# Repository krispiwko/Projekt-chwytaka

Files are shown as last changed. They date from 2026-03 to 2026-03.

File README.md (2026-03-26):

Autor: Krzysztof Piwkowski

Opis projektu:
Chwytak wykonany na zajęcia z Prototypowania konstrukcji w technice druku 3D i CNC.
Schemat chwytaka dostarczony od prowadzącego zajęcia. Chwytak ma za zadanie
podnieść drewniany obiekt w kształcie walca o średnicy 60mm i wysokości 150mm.
Do zaprojektowania struktury fizycznej został wykorzystany program Autodesk Inventor.
Obliczenia funkcji kinematycznych wykonano w Matlabie. Widok chwytaka można odtworzyć
kopiując pliki z folderu "Pliki chwytaka" do darmowego viewera firmy autodesk:
viewer.autodesk.com
Szczegółowe informacje znajdują się w sprawozdaniu zamieszczonym na repozytorium.

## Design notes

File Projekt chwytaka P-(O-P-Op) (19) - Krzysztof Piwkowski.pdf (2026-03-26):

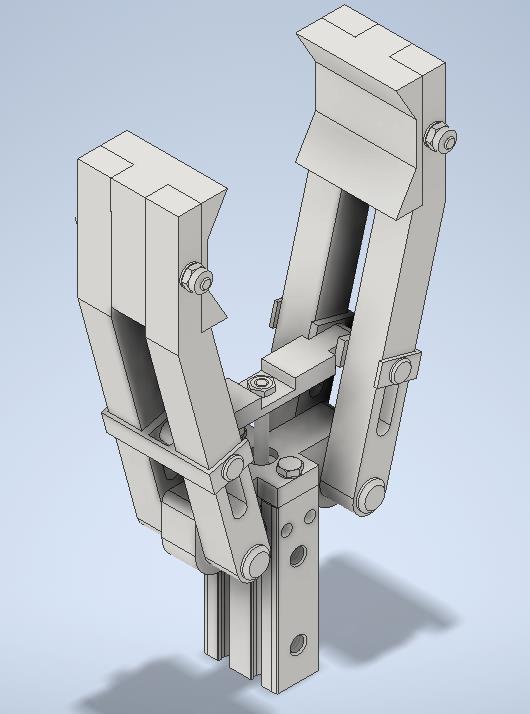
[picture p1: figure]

# PROJEKT CHWYTAKA P-(O-P-Op)

## Jednostka: AGH WEAIIB – Automatyka i Robotyka – Gr. 7

Data wykonania: 7 czerwca 2024r.

## Autor: Krzysztof Piwkowski

## Spis treści

## 1. O projekcie

Przedstawiony w tym projekcie chwytak był wykonany według podanego poniżej schematu:

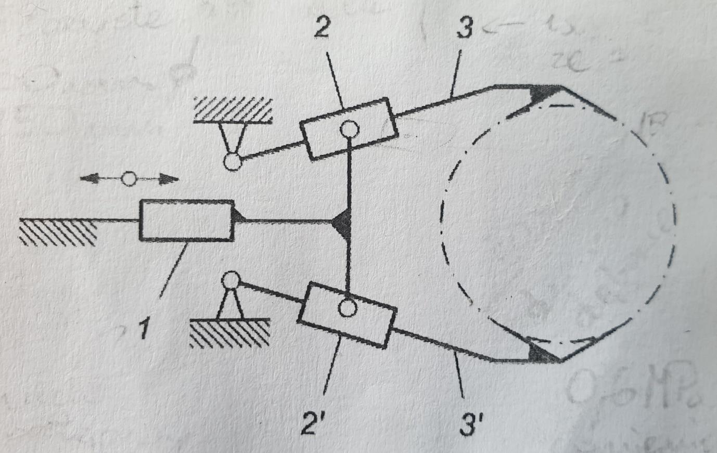
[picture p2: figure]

Chwytak ma parametry przystosowane do podnoszenia przedmiotu z powietrzosuchego drewna dębowego w kształcie walca o średnicy 60mm i wysokości 150mm. Jest to chwytak siłowo-kształtowy o siłowniku postępowym z parami kinematycznymi – obrotowej, postępowej i prowadnicy z możliwością obrotu (P-(O-P-Op)). Ostatecznie ruch szczęki chwytaka prowadzony jest po okręgu. Znając te informacje oraz ilość użytych w projekcie par kinematycznych możemy dokonać analizy ruchliwości chwytaka:

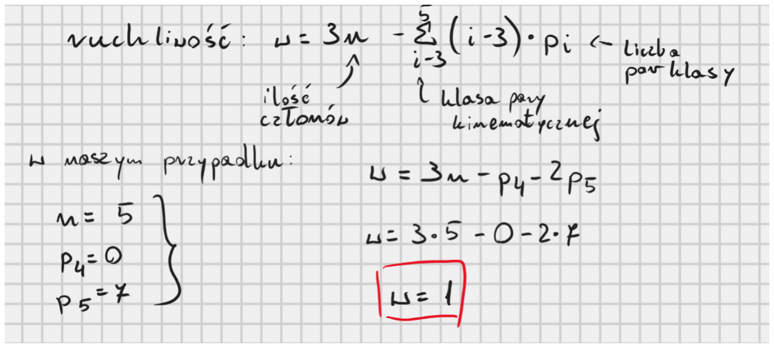
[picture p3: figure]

Ruchliwość rzędu 1 oznacza, że wprawienie w ruch jednego członu wprawia w ruch pozostałe.

## 2. Analiza geometryczna

Aby dokonać analizy geometrycznej wykonałem schemat chwytaka w rozmiarze rzeczywistym. Następnie wyznaczyłem minimalny kąt wychylenia potrzebny na wypuszczenie przedmiotu, co pozwoliło wyznaczyć skok siłownika:

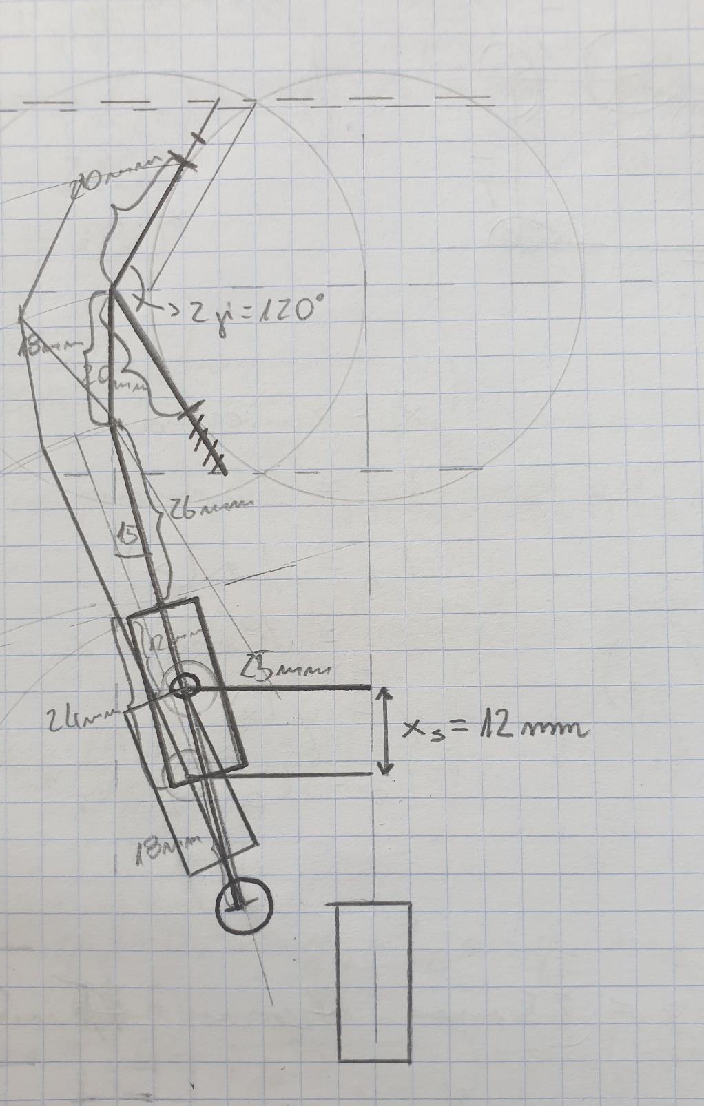
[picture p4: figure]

Analiza geometryczna pozwoliła wyznaczyć skok siłownika na 12mm, jednak najczęściej dostępne są jedynie siłowniki o skoku 10 lub 15mm. Aby przedmiot mógł swobodnie wypaść, należało wybrać siłownik o większym skoku – 15mm. Rysunek pozwolił także przyjąć długości odpowiednich elementów chwytaka oraz kąt rozstawienia szczęki (zaznaczone na rysunku).

## 3. Charakterystyka siłowa

Charakterystyka siłowa polegała na związanie ze sobą sił działających na poszczególne elementy chwytaka tak, aby przenieść siłę chwytu na siłę siłownika. Parametry potrzebne do wyznaczenia odpowiednich wartości przyjęto jako:

- współczynnik tarcia stal – drewno: 0,55 [1]
- gęstość drewna dębowego minimalna i maksymalna: 710 i 800 kg/m^3 [2] Wyznaczenie minimalnej siły chwytu, aby bezpiecznie utrzymać obiekt prezentuje się następująco:

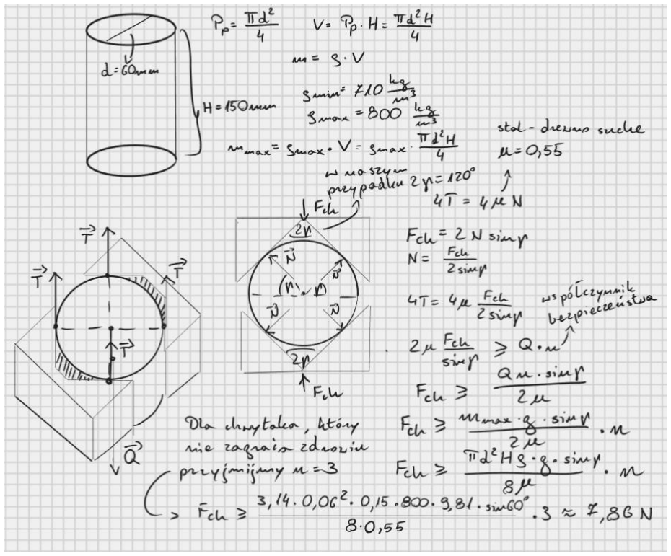
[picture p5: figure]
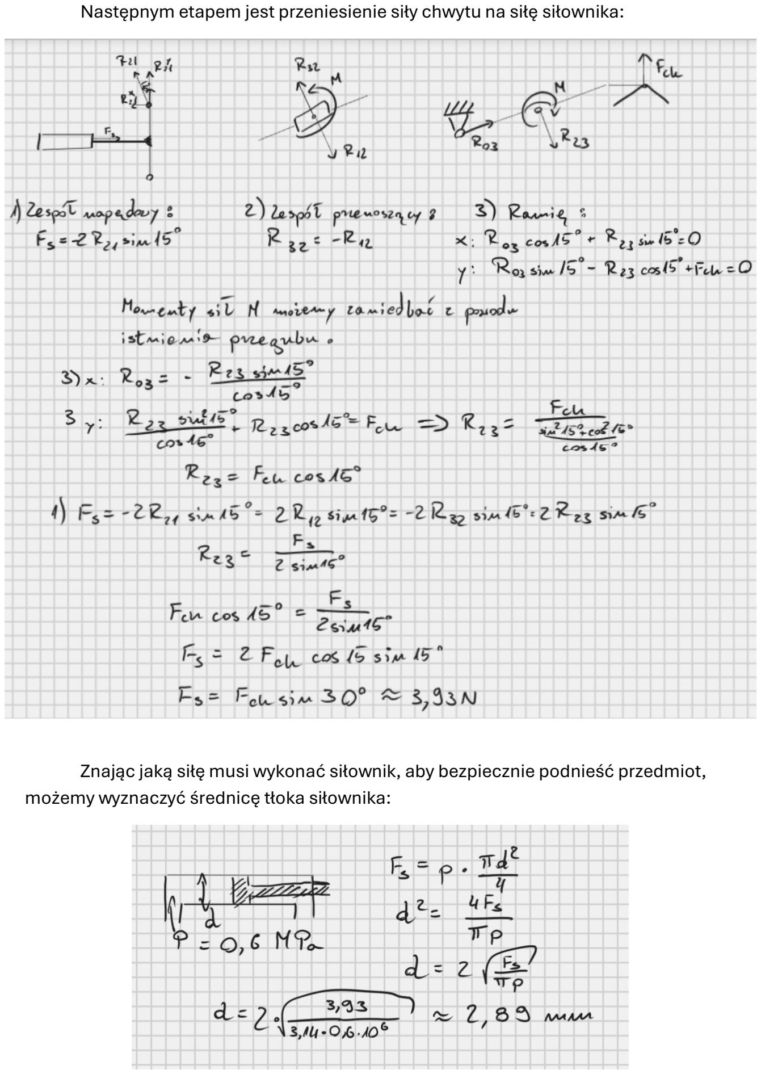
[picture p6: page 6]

Następnym etapem jest przeniesienie siły chwytu na siłę siłownika:

Znając jaką siłę musi wykonać siłownik, aby bezpiecznie podnieść przedmiot, możemy wyznaczyć średnicę tłoka siłownika:

Znając skok (15mm) i średnicę tłoka(2,89mm) możemy przejść do dobrania odpowiedniego siłownika. Wybierając kompaktowy siłownik, który jest łatwy w montażu, o skoku 15mm okazuje się, że dostępny model jest tylko o średnicy tłoka od 6mm. Wybierając siłownik o takiej średnicy zwiększamy siłę chwytu czterokrotnie. Dlatego przyjęty na początku współczynnik bezpieczeństwa także zwiększy się czterokrotnie (n = 12).
Ostatecznie wybrany przeze mnie chwytak można znaleźć na stronie internetowej Festo:

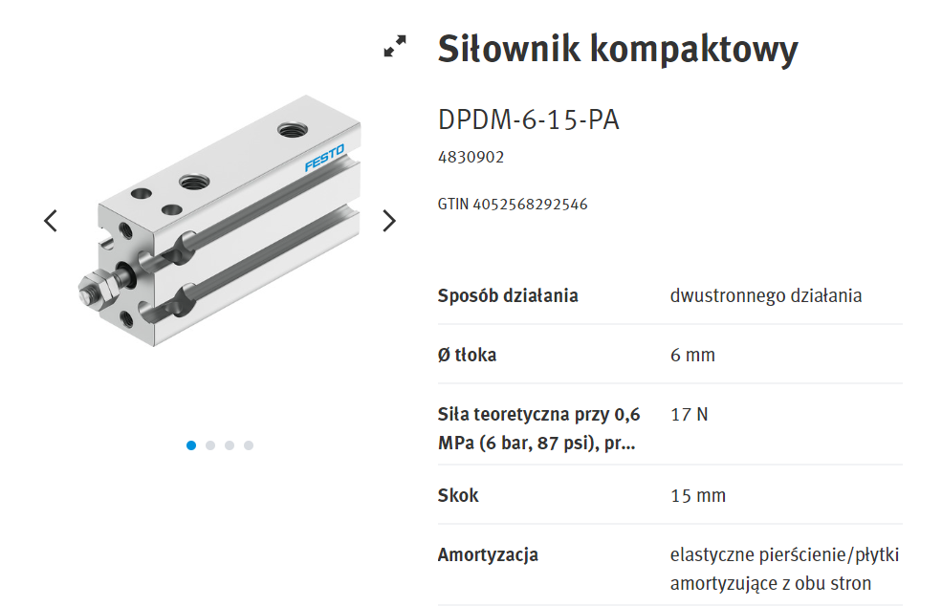
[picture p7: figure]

Znając już, jaki model chwytaka będzie użyty, można przejść do utworzenia ostatecznego modelu całego chwytaka. Do zbudowania chwytaka użyłem programu Autodesk Inventor. Model 3D widnieje na stronie tytułowej, tutaj zamieszczony zostaje rysunek złożeniowy:

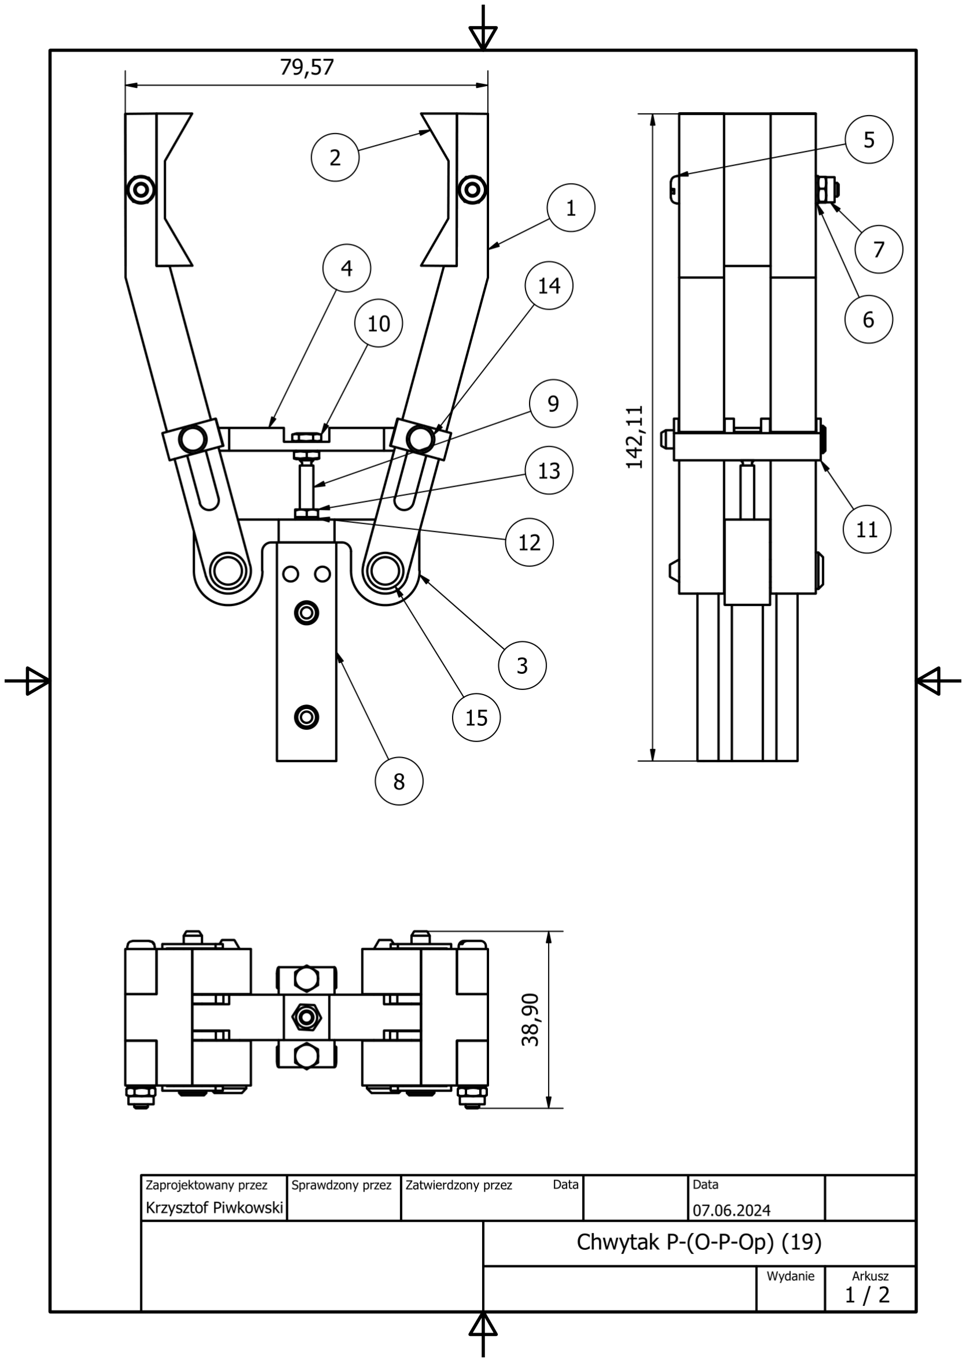
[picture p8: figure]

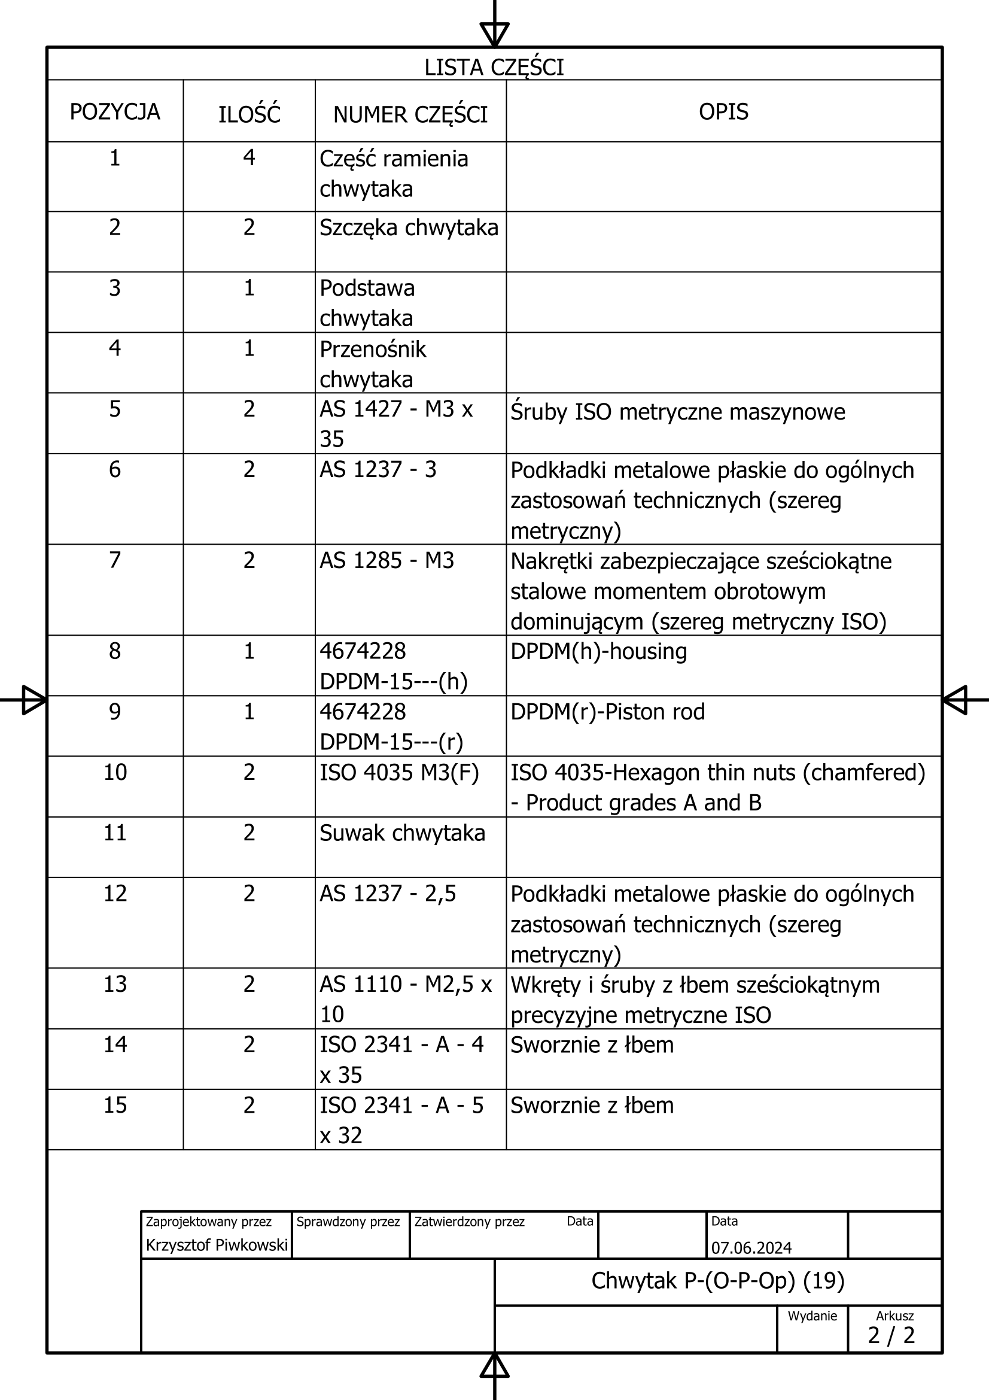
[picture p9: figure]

## 4. Charakterystyka przesunięciowa i prędkościowa

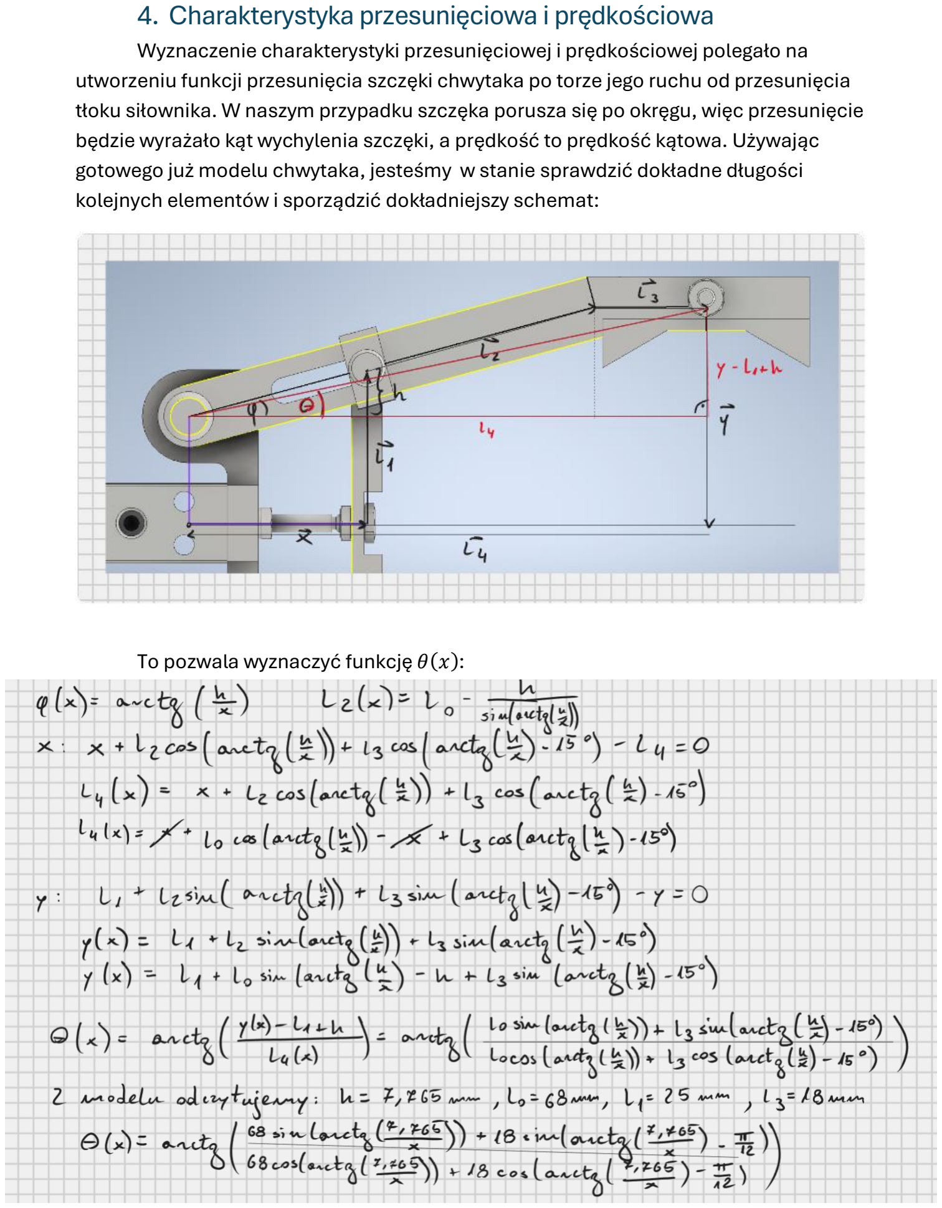
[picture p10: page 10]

Wyznaczenie charakterystyki przesunięciowej i prędkościowej polegało na utworzeniu funkcji przesunięcia szczęki chwytaka po torze jego ruchu od przesunięcia tłoku siłownika. W naszym przypadku szczęka porusza się po okręgu, więc przesunięcie będzie wyrażało kąt wychylenia szczęki, a prędkość to prędkość kątowa. Używając gotowego już modelu chwytaka, jesteśmy w stanie sprawdzić dokładne długości kolejnych elementów i sporządzić dokładniejszy schemat:

To pozwala wyznaczyć funkcję θ(x):

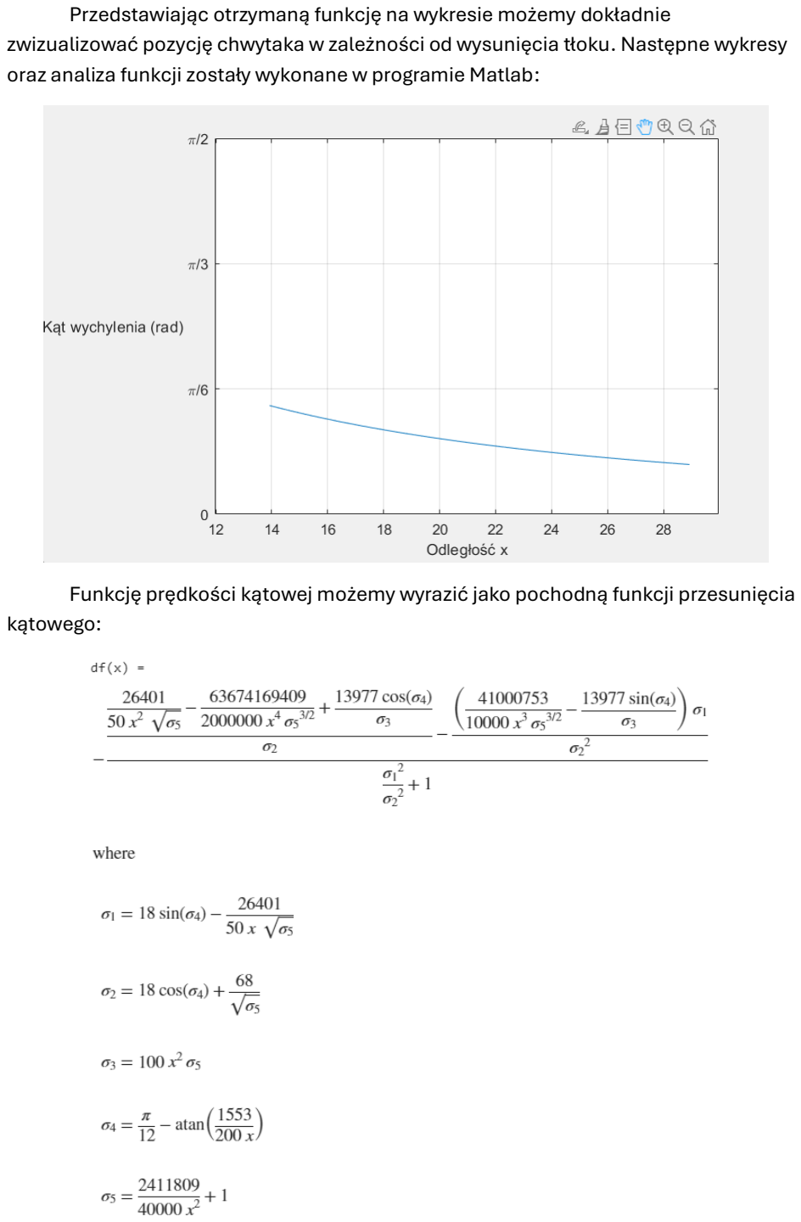
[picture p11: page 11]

Przedstawiając otrzymaną funkcję na wykresie możemy dokładnie zwizualizować pozycję chwytaka w zależności od wysunięcia tłoku. Następne wykresy oraz analiza funkcji zostały wykonane w programie Matlab:

Funkcję prędkości kątowej możemy wyrazić jako pochodną funkcji przesunięcia kątowego:

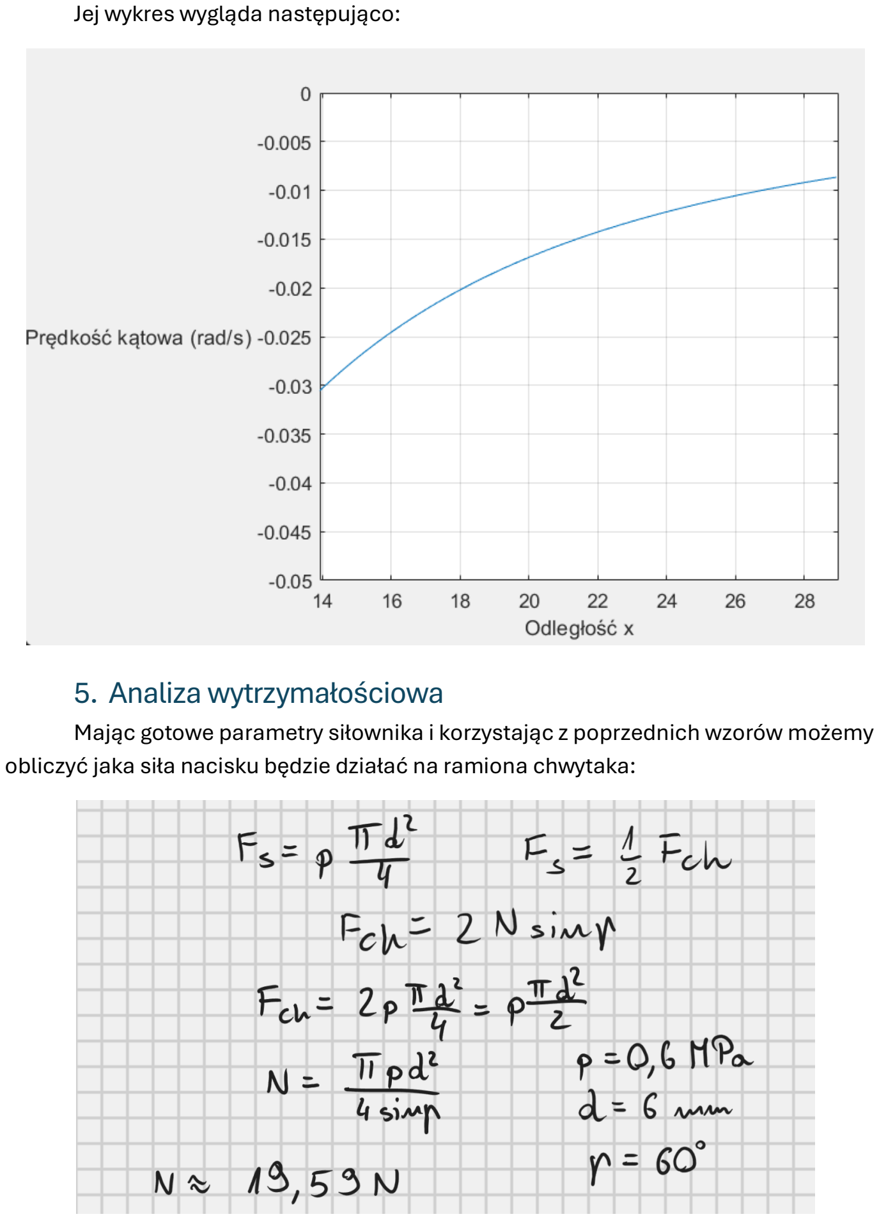
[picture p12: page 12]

Jej wykres wygląda następująco:

## 5. Analiza wytrzymałościowa

Mając gotowe parametry siłownika i korzystając z poprzednich wzorów możemy obliczyć jaka siła nacisku będzie działać na ramiona chwytaka:

Korzystając z obliczonej siły wykonajmy analizę naprężeń w programie Inventor:

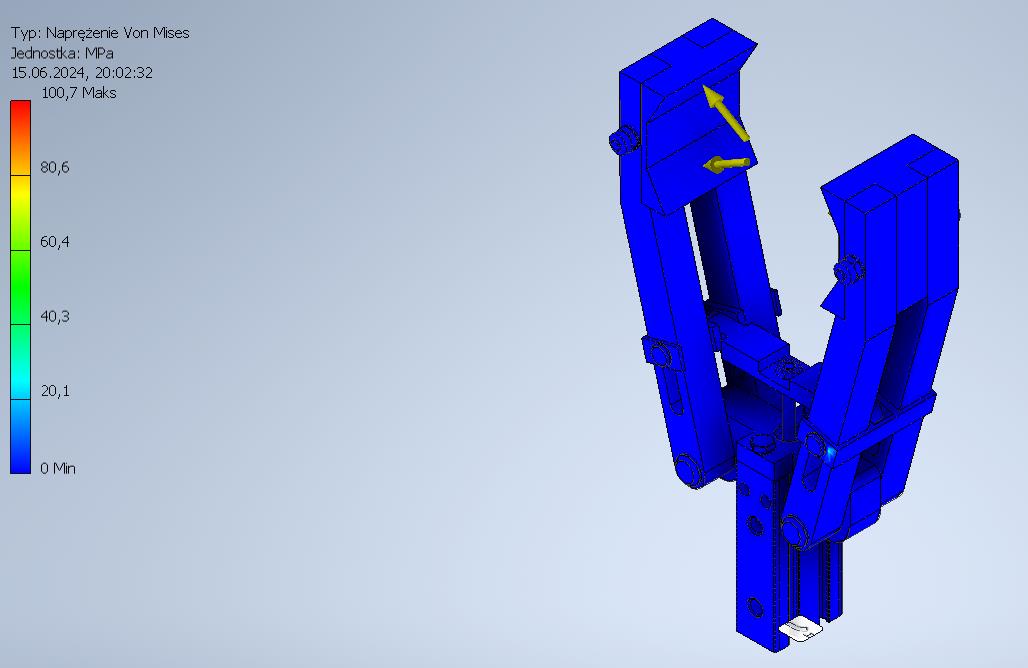
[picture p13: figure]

Jak widać na skali po lewej stronie, maksimum naprężeń wynosi 100,7MPa, podczas gdy wartości współczynników wytrzymałościowych stali węglowej, z jakiej wykonany jest chwytak, prezentują się następująco:

Informacje te znajdują się jako domyślne wartości w programie Inventor. Widać zatem, że generowane naprężenia nie spowodują uszkodzenia chwytaka.
Możemy także zbadać czy siła nacisku, jaką chwytak wywiera na przedmiot, spowoduje uszkodzenie drewna dębowego. Aby to zrobić, przyjmijmy, że szerokość pola powierzchni styczności między okrągłym przedmiotem a szczęką to 1mm, podczas gdy długość szczęki wynosi 30mm. Wówczas:

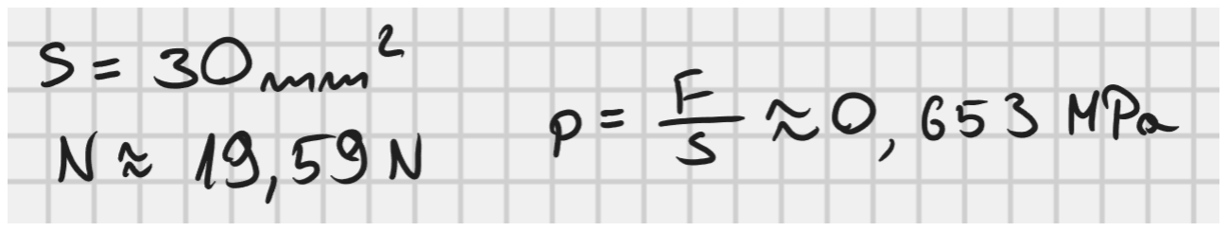
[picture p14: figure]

Wytrzymałość drewna dębowego w najgorszym przypadku wynosi 11MPa [3], więc siła nacisku nie uszkodzi materiału.

## 6. Parametry

Ostateczne zestawienie najważniejszych parametrów związanych z pracą chwytaka:

Średnica
tłoka [mm]

Czynnik
roboczy

Ciśnienie pracy
[MPa]
Siła chwytu [N] | Typ chwytaka | Promień podnoszonego
obiektu walcowego [mm]
6 powietrze | 0,6 | 33,93 siłowo - kstzałtowy | 60
Minimalne wychylenie kątowe [°] | Maksymalne wychylenie kątowe [°] | Minimalna odległość szczęki od środka [mm] | Maksymalna odległość szczęki od środka [mm]
11,9 | 26 | 34,87 | 54,72

## 7. Bibliografia

[1] “Jak dobrać właściwy chwytak? » Chwytaki przemysłowe.” Accessed: Jun. 15, 2024. [Online]. Available: http://www.chwytaki.com.pl/artykul/4552/jak-dobracwlasciwy-chwytak/
[2] “Otwarta Encyklopedia Leśna [g:gestosc-drewna].” Accessed: Jun. 15, 2024. [Online]. Available:
https://www.encyklopedia.lasypolskie.pl/doku.php?id=g:gestosc-drewna
[3] A. Lis and P. Lis, “CHARAKTERYSTYKA WYTRZYMAŁOŚCI DREWNA JAKO JEGO PODSTAWOWEJ WŁAŚCIWOŚCI MECHANICZNEJ.”

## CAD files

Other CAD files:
Pliki Chwytak/4674228 DPDM-15---(h).ipt
Pliki Chwytak/4674228 DPDM-15---(r).ipt
Pliki Chwytak/4830902 DPDM-6-15-PA---(0).iam
Pliki Chwytak/AS 1110 - M2,5 x 10.ipt
Pliki Chwytak/AS 1237 - 2,5.ipt
Pliki Chwytak/AS 1237 - 3.ipt
Pliki Chwytak/AS 1285 - M3(2).ipt
Pliki Chwytak/AS 1427 - M3 x 35(3).ipt
Pliki Chwytak/Chwytak.iam
Pliki Chwytak/Część ramienia chwytaka.ipt
Pliki Chwytak/Część ramienia chwytaka_MIR1.ipt
Pliki Chwytak/Część ramienia chwytaka_MIR1_MIR.ipt
Pliki Chwytak/Część ramienia chwytaka_MIR2.ipt
Pliki Chwytak/ISO 2341 - A - 4 x 35ISO.ipt
Pliki Chwytak/ISO 2341 - A - 5 x 32ISO.ipt
Pliki Chwytak/ISO 4035 M3(F).ipt
Pliki Chwytak/Podstawa chwytaka.ipt
Pliki Chwytak/Połączenie sworzniowe1.iam
Pliki Chwytak/Połączenie sworzniowe2.iam
Pliki Chwytak/Połączenie sworzniowe3.iam
Pliki Chwytak/Połączenie sworzniowe4.iam
Pliki Chwytak/Przenośnik chwytaka.ipt
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
